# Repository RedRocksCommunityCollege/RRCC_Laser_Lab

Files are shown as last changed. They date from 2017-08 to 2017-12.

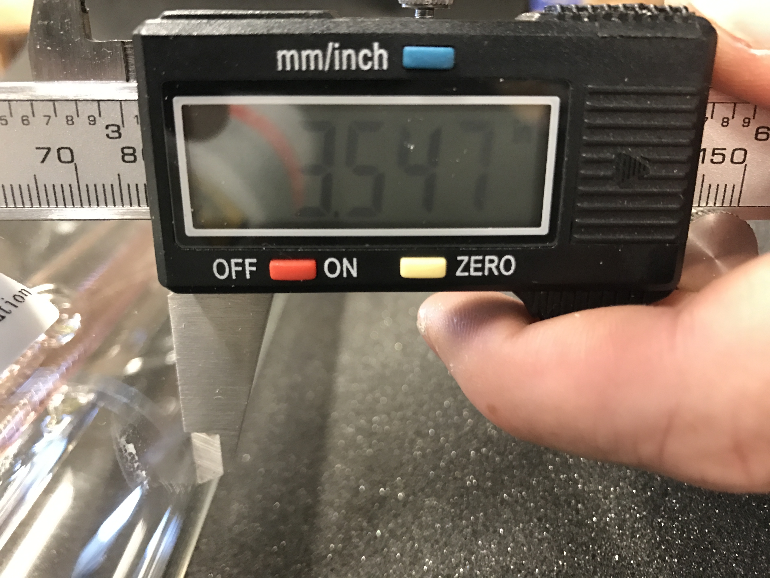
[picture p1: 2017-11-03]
Laser_Build_Pictures/47_Tube_Right_Middle_Outside_Diameter_Detail.JPG

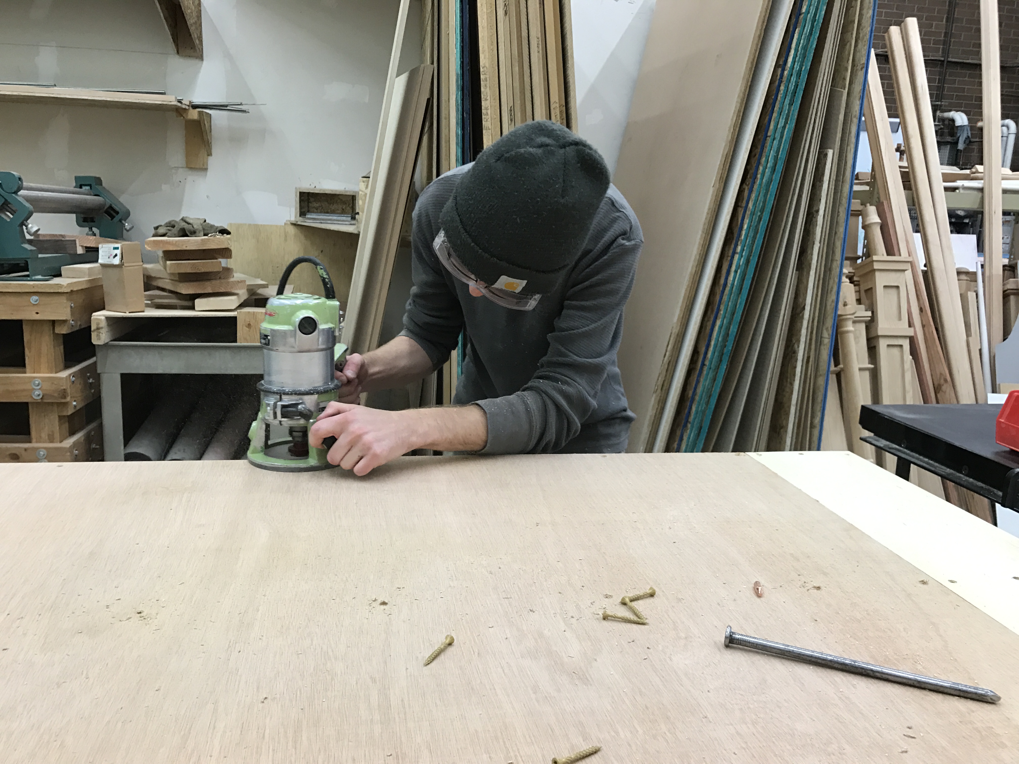
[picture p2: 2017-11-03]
Laser_Build_Pictures/6_Laser_Table_Build.JPG

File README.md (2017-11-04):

## Welcome to the RRCC Laser GitHub Page. Below you will find links and information for the attached repo.

**Background Information** : Over the fall of 2017 the students of Red Rocks Community College designed and build an 80 watt computer controlled laser cutter. The process took around 12 weeks working 4 to 8 hours a week. The parts were ordered from:

* Gantry parts: https://openbuilds.com/
* Laser parts: http://www.lightobject.com/
* Building table parts: https://www.homedepot.com/
* Other: https://www.amazon.com/

***

The parts list can be found here: [Parts List](https://github.com/RedRocksCommunityCollege/RRCC_Laser_Lab/tree/master/Parts_List). We have included both an Excel and .csv file for both the gantry and laser parts list. 

The image files can be found here: [Laser build pictures](https://github.com/RedRocksCommunityCollege/RRCC_Laser_Lab/tree/master/Laser_Build_Pictures). The images have a basic description in the file name. They are in chronological order and images that have a measurement in it should have a close-up that follows the wide image.  

The project timeline and To Do can be found here: [Timeline and ToDo](https://github.com/RedRocksCommunityCollege/RRCC_Laser_Lab/projects/1). In the Projects tab you will find all the ongoing issues that we are working on. If you would like to work on one of these isseus feel free to assign the issue to yourself and move it the the active column. Once you are finished please move the issue to the Done column and mark the issue as closed in the issues tab. We are using the following code for issues:

* **Bug** is software related issue (Eg make a wiki, Work on GitHub, add files...)
* **Enhancement** is for physical modifications to the Laser cutter.
* **Question** is for elements that need leadership approval. 

***

The tube that we are using is a [W2 Reci laser tube](http://www.recilaser.com/en/index.php?m=&c=Index&a=show&catid=7&id=66) that has a wattage of 90. We are using an [800 Watt chiller](http://www.lightobject.com/LightObject-800W-Water-Chiller-for-CO2-Laser-Machine-AC110V-60Hz-P996.aspx) and a [Smoothieboard v1](http://smoothieware.org/smoothieboard) control board. 

  

***
The main goal of the laser cutter is to be a tool for student working in the lab as well as a tool for students to use for projects in classes. The cutter will be able to cut wood and leather and engrave metal. We are also hoping to be able to...

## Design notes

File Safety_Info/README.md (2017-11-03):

# Safety_Info
These are all the files from Reci. We are using the W2 laser in this build. [Here is a link to the product page](http://www.recilaser.com/en/index.php?m=&c=Index&a=show&catid=7&id=66)

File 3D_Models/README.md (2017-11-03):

# 3D-Models

These files are used for virtual assemblies, visualizing parts, and creating test simulations

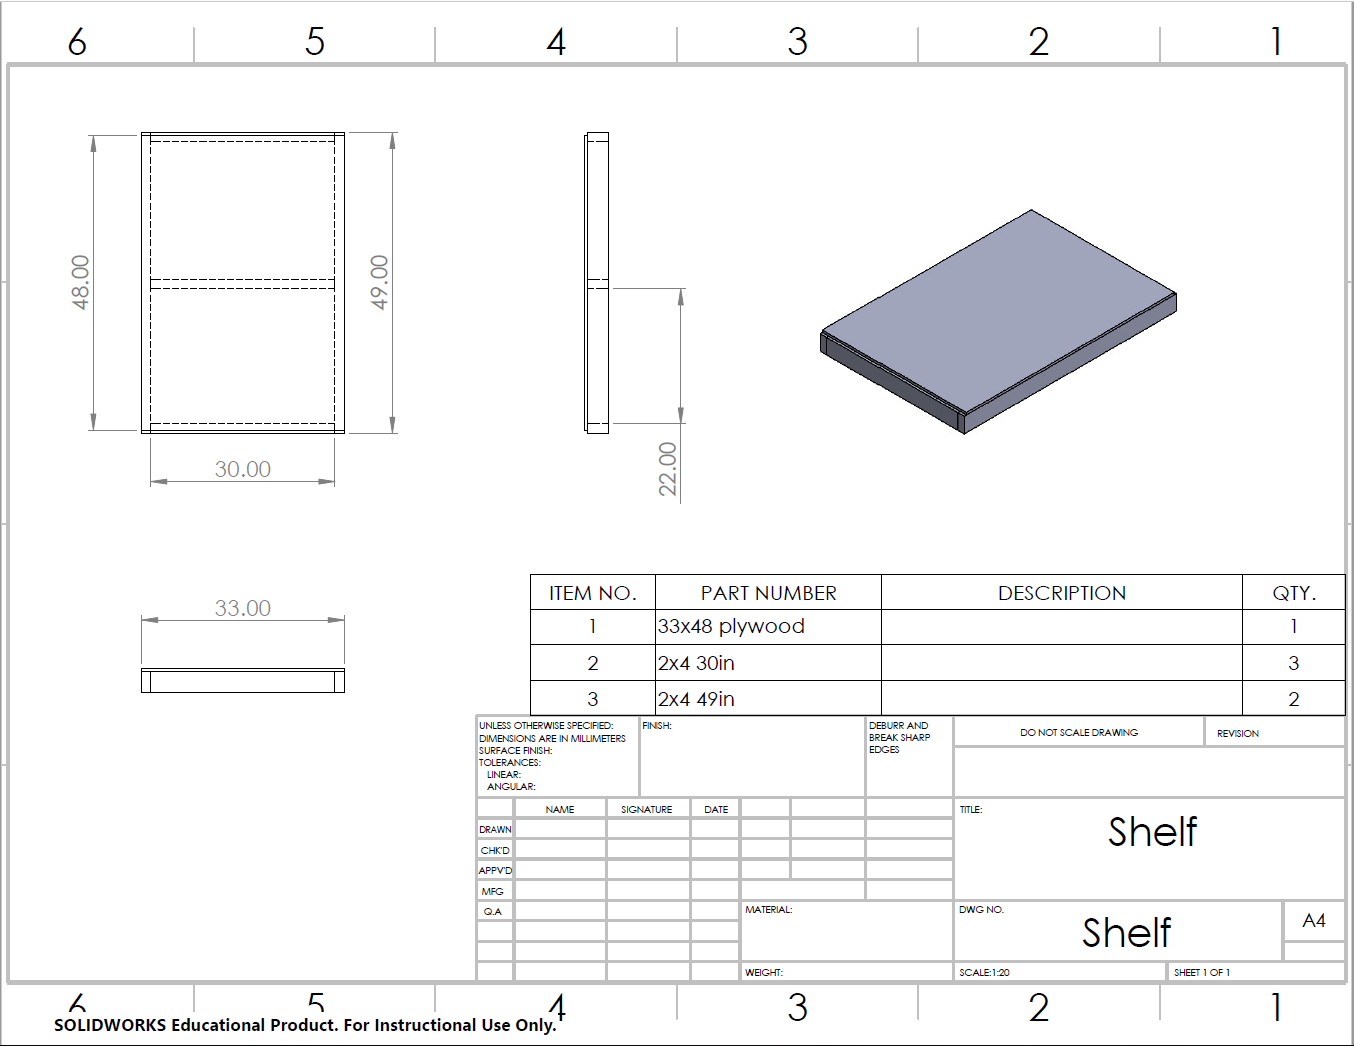
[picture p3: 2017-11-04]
Tech_Drawings_Specifications/Shelft.PNG

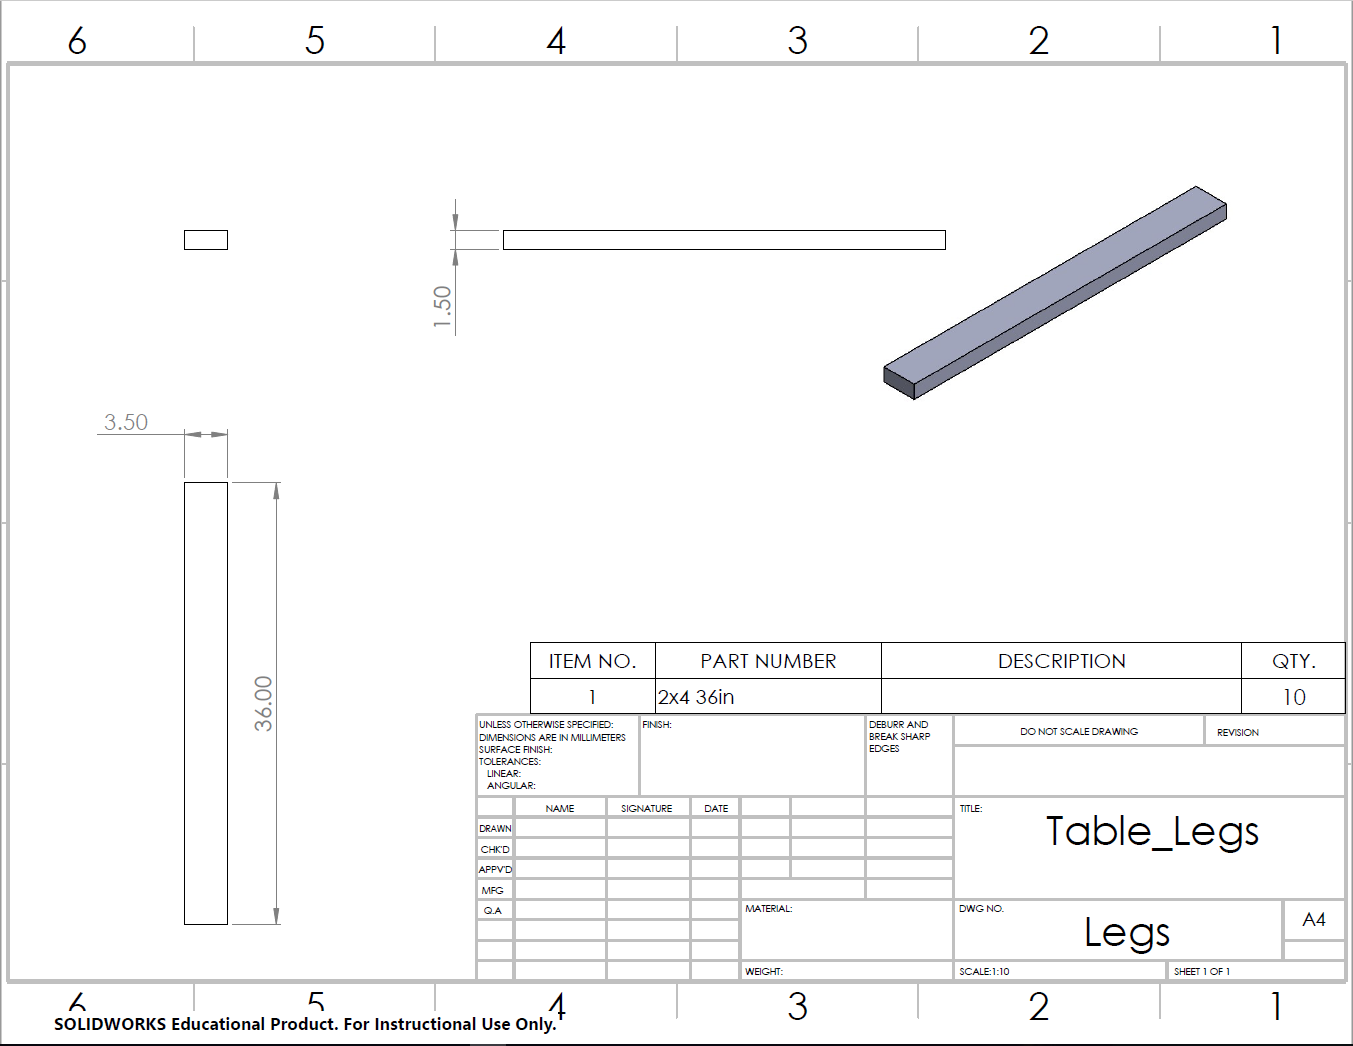
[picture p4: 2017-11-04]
Tech_Drawings_Specifications/Leg.PNG

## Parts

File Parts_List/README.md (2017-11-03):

# Parts_List

List of all necessary components for both the gantry and laser parts

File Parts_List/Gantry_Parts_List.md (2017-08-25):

Item,	Item, Description,	URL,	Quantity, 	Unit Price,	Total,
C-Beam Linear Actuator Bundle	1000mm, Include Motor,	http://openbuildspartstore.com/c-beam-linear-actuator-bundle/ ,	3,	139.95,	419.85,
V-Slot Linear Rail 20mm x 60mm	20mm x 60mm, 1000mm, Silver	http://openbuildspartstore.com/v-slot-linear-rail/ ,	8,	17,	136,
V-Slot Linear Rail 20mm x 80mm	20mm x 80mm, 1000mm, Silver	http://openbuildspartstore.com/v-slot-linear-rail/ ,	1,	22,	22,
Black Angle Corner Connector	Corner Connectors,	http://openbuildspartstore.com/black-angle-corner-connector/ ,	50,	2.75,	137.5,
Cube Corner Connector	3-Way Corner Connector,	http://openbuildspartstore.com/cube-corner-connector/ ,	15, 3.25,	48.75,
Tee Nuts (25 Pack),	Tee Nuts,	http://openbuildspartstore.com/tee-nuts-25-pack/ ,	5,	4.95,	24.75,
Smothieboard 4x	Control Board,	https://shop.uberclock.com/collections/smoothie/products/smoothieboard-4x ,	1,	129.95,	129.95,
Low Profile M5 Screws	8mm M5 Screw,	http://openbuildspartstore.com/low-profile-screws-m5/ ,	4,	3 , 12,
12V/29A Meanwell Power Supply	Power, supply for motors/ logic board,	http://openbuildspartstore.com/12v-29a-meanwell-power-supply/ ,	1,	47.95,	47.95

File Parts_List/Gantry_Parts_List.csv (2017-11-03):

Item | Item Description | URL | Quantity | Unit Price | Total
C-Beam Linear Actuator Bundle | 1000mm, Include Motor | http://openbuildspartstore.com/c-beam-linear-actuator-bundle/ | 3 | 139.95 | 419.85
V-Slot Linear Rail 20mm x 60mm | 20mm x 60mm 1000mm Silver | http://openbuildspartstore.com/v-slot-linear-rail/ | 8 | 17 | 136
V-Slot Linear Rail 20mm x 80mm | 20mm x 80mm 1000mm Silver | http://openbuildspartstore.com/v-slot-linear-rail/ | 2 | 22 | 44
Black Angle Corner Connector | Corner Connectors | http://openbuildspartstore.com/black-angle-corner-connector/ | 75 | 2.75 | 206.25
Cube Corner Connector | 3-Way Corner Connector | http://openbuildspartstore.com/cube-corner-connector/ | 15 | 3.25 | 48.75
Tee Nuts (25 Pack) | Tee Nuts | http://openbuildspartstore.com/tee-nuts-25-pack/ | 7 | 4.95 | 34.65
Smothieboard 4x | Smoothieboard 5xC v1.1 | http://openbuildspartstore.com/smoothieboard-5xc-v1-1/ | 2 | 165.95 | 331.9
Low Profile M5 Screws | 8mm M5 Screw | http://openbuildspartstore.com/low-profile-screws-m5/ | 7 | 3 | 21
12V/29A Meanwell Power Supply | Power supplie for motors/ logic board | http://openbuildspartstore.com/12v-29a-meanwell-power-supply/ | 1 | 47.95 | 47.95
V-Slot Linear Rail 20mm x 60mm | 20mm x 60mm 1500mm Silver | http://openbuildspartstore.com/v-slot-linear-rail/ | 2 | 23 | 46
90 Degree Joining Plate | Connect X axis to Y axis | http://openbuildspartstore.com/90-degree-joining-plate/ | 2 | 4.8 | 9.6
 |  |  |  |  | 1345.95

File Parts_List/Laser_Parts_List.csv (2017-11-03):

Item Description | SKU | URL | Quantity | Unit Price | Total
80W~100W PWM CO2 Laser Power Supply (AC110V) | LSR-JN80WCO2-1V | www.lightobject.com | 1 | 285 | 285
LightObject 800W Water Chiller for CO2 Laser Machine (AC110V 60Hz) | WC-LO850W1V6 | www.lightobject.com | 1 | 525 | 525
CO2 10600nm Laser Eyes Protection Glasses/Goggle. CE certified | LSR-EP4 | www.lightobject.com | 3 | 35 | 105
Laser Head Mount for 25mm Mirror & 20mm Focus Lens. LR Type | LSR-YT-HD2520LR | www.lightobject.com | 1 | 59 | 59
Improved 20mm ZnSe Focus lens (F50.8mm) | LSR-LEN20ZN5I | www.lightobject.com | 1 | 35 | 35
Pro 20mm Reflection Mirror Mount for Co2 Laser Machine | LSR-PR20M2D | www.lightobject.com | 34.5 | 2 | 69
20 mm Molybdenum (MO) Reflection Mirror | LSR-MIR20MO | www.lightobject.com | 2 | 27.5 | 55
25mm High Quality Si Plated Reflection Mirror | LSR-MIR25MSI | www.lightobject.com | 1 | 29.5 | 29.5
High Quality RECI W2 80W CO2 Sealed Laser Tube(10000Hrs) | LSR-JLDHQ80WCO2 | www.lightobject.com | 1 | 650 | 650
http://www.lightobject.com/3-digit-Mini-Blue-LED-1A-Current-Meter-P641.aspx | EPM-3D1AB | www.lightobject.com | 1 | 9.5 | 9.5

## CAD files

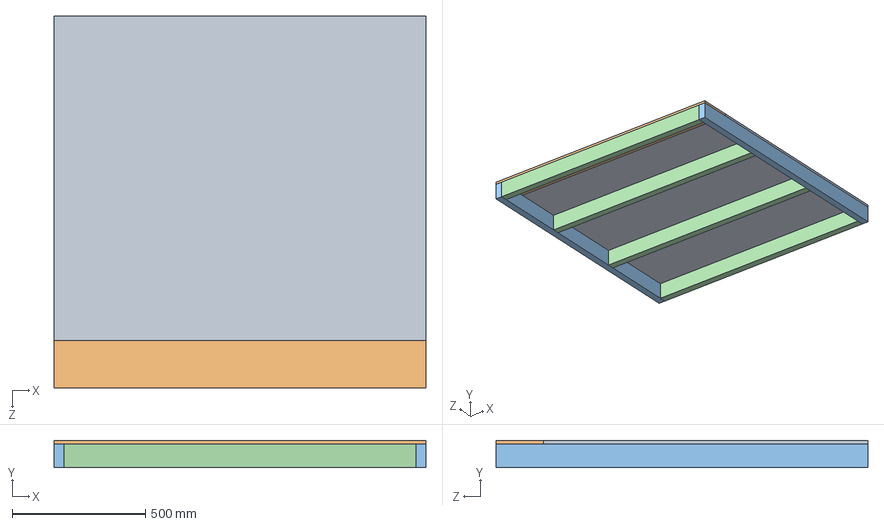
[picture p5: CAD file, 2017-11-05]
3D_Models/Top.SLDASM
1397.0 x 101.6 x 1397.0 mm
48x55 plywood
7x55 plywood
2x4 55in x 2
2x4 52in x 4

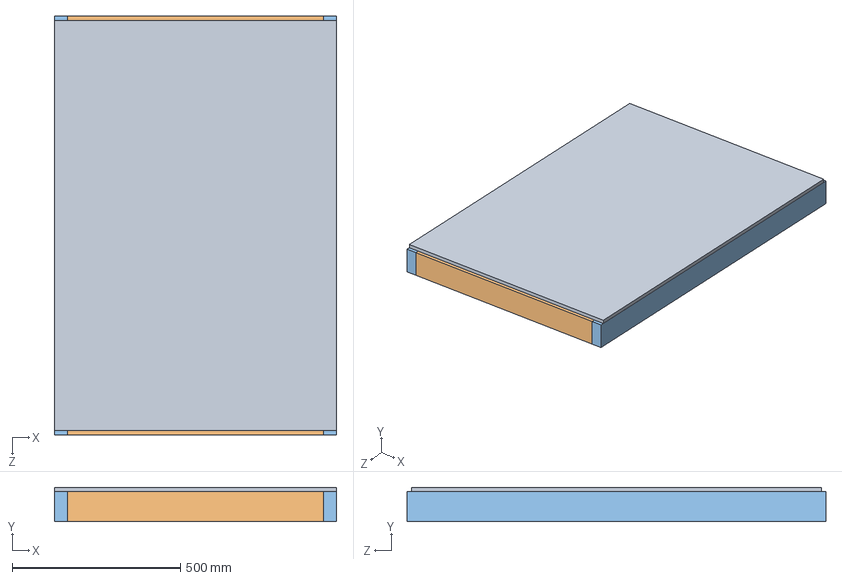
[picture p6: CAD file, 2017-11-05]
3D_Models/Shelf.SLDASM
838.2 x 101.6 x 1244.6 mm
33x48 plywood
2x4 30in x 3
2x4 49in x 2

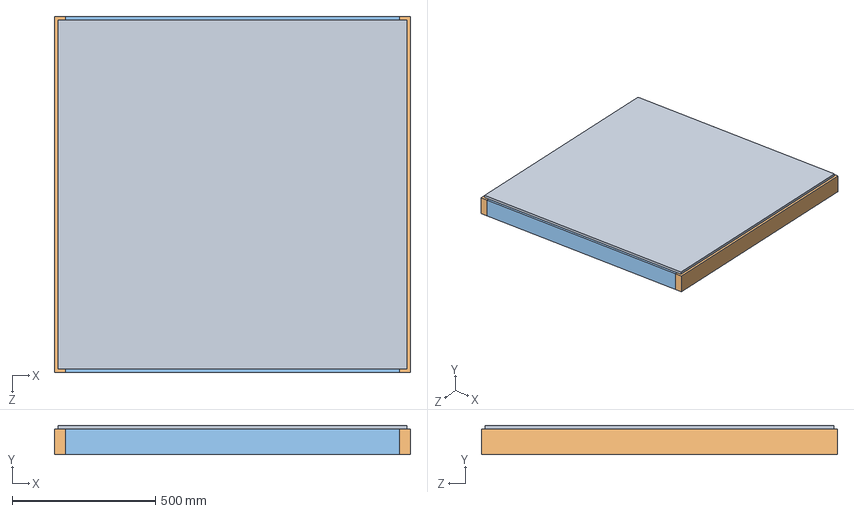
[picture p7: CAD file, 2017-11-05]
3D_Models/Bottom_Shelf.SLDASM
1244.6 x 101.6 x 1244.6 mm
48x48 plywood
2x4 49in x 2
2x4 46in x 3

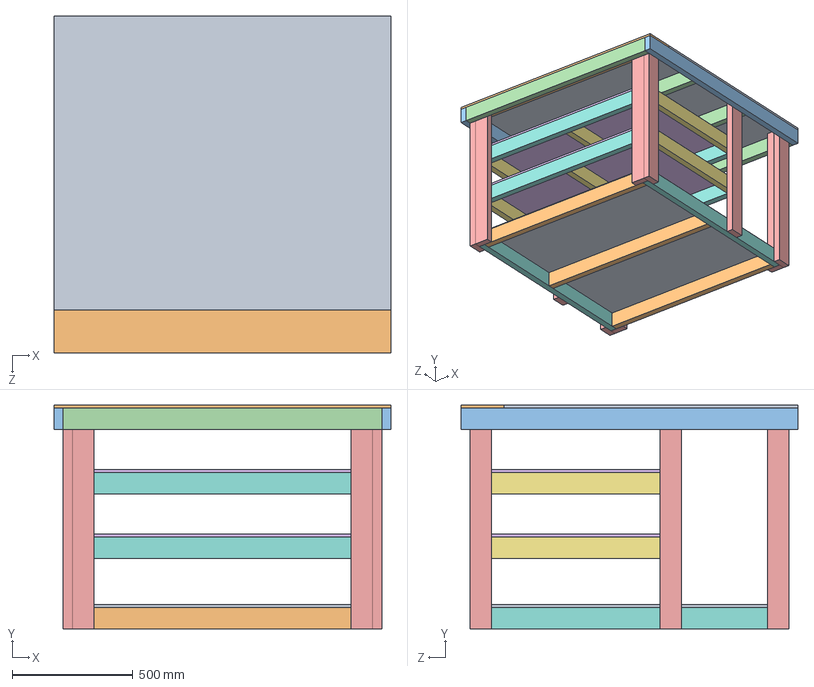
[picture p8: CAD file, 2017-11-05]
3D_Models/CNC_Laser_Table_Assembly.SLDASM
1397.0 x 927.1 x 1397.0 mm
48x55 plywood
7x55 plywood
2x4 55in x 2
2x4 52in x 4
2x4 36in x 10
33x48 plywood x 2
2x4 30in x 6
2x4 49in x 6
48x48 plywood
2x4 46in x 3

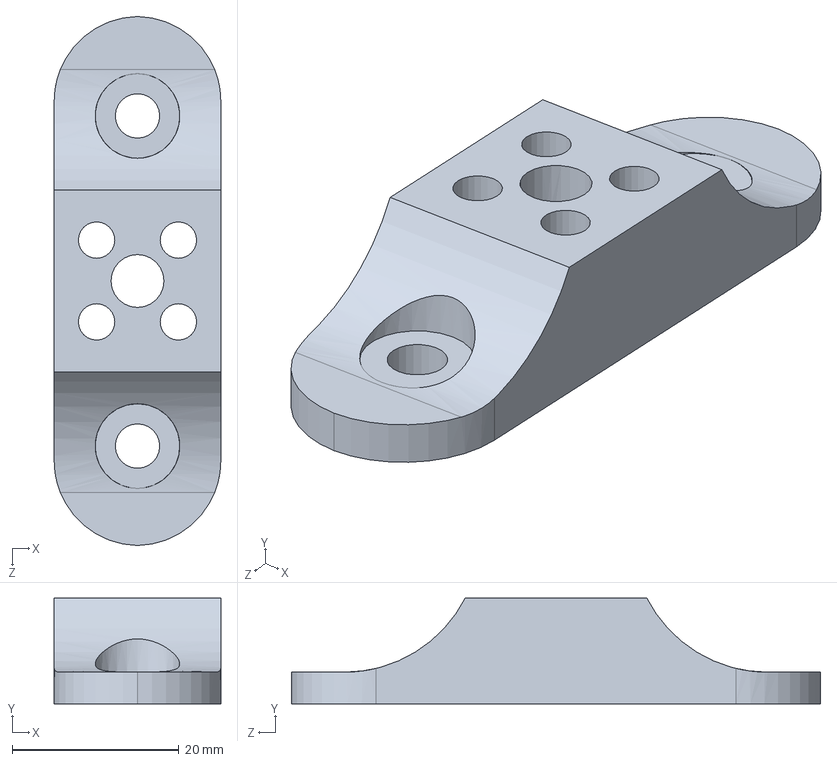
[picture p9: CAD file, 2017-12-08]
3D-Printed_Components/Mirror_Mount_Y_Axis.SLDPRT
20.0 x 12.7 x 63.5 mm

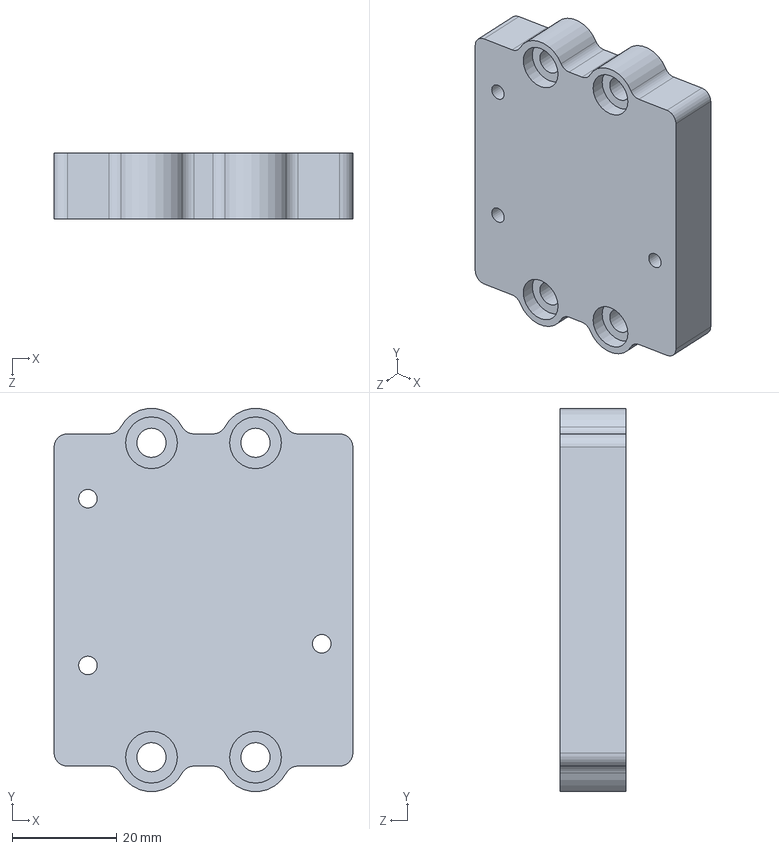
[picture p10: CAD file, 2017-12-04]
3D-Printed_Components/CNC_Laser_Adapter_Plate.SLDPRT
57.1 x 73.2 x 12.7 mm

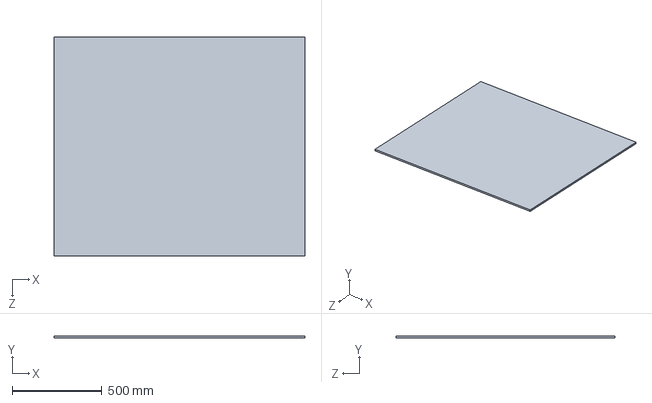
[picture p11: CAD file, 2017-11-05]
3D_Models/48x55 plywood.SLDPRT
1397.0 x 12.7 x 1219.2 mm

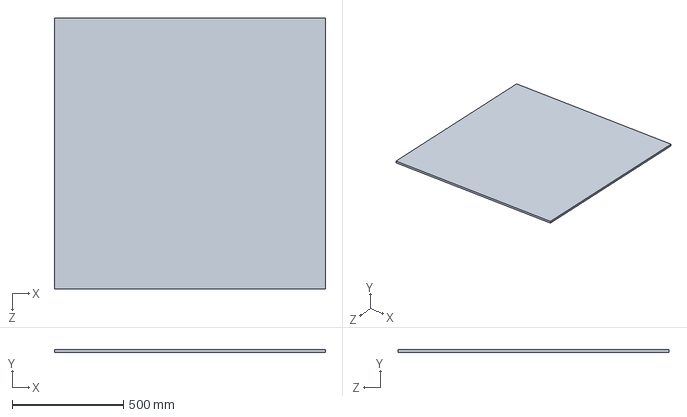
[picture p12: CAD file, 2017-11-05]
3D_Models/48x48 plywood.SLDPRT
1219.2 x 12.7 x 1219.2 mm

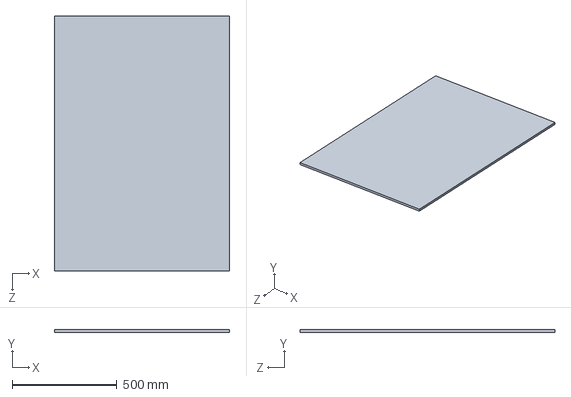
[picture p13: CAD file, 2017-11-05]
3D_Models/33x48 plywood.SLDPRT
838.2 x 12.7 x 1219.2 mm

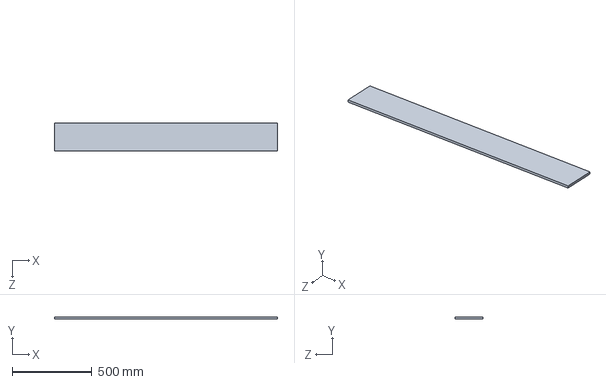
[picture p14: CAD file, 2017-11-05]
3D_Models/7x55 plywood.SLDPRT
1397.0 x 12.7 x 177.8 mm

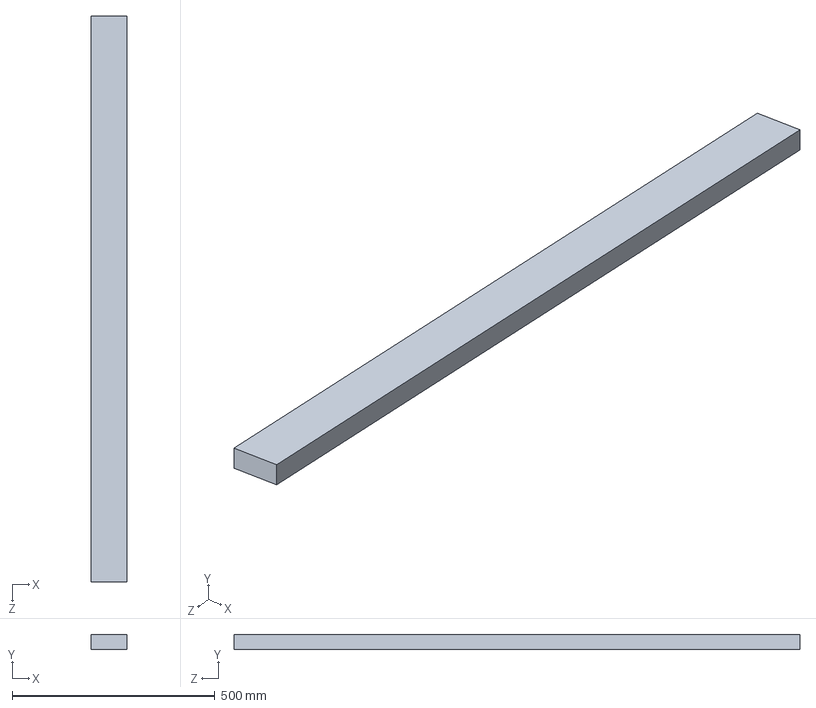
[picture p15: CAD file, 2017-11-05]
3D_Models/2x4 55in.SLDPRT
88.9 x 38.1 x 1397.0 mm

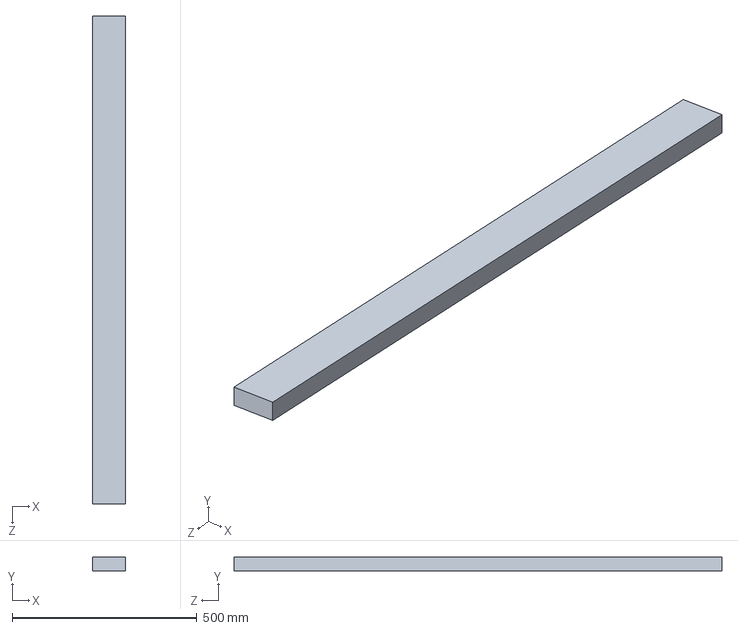
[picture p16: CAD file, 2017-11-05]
3D_Models/2x4 52in.SLDPRT
88.9 x 38.1 x 1320.8 mm

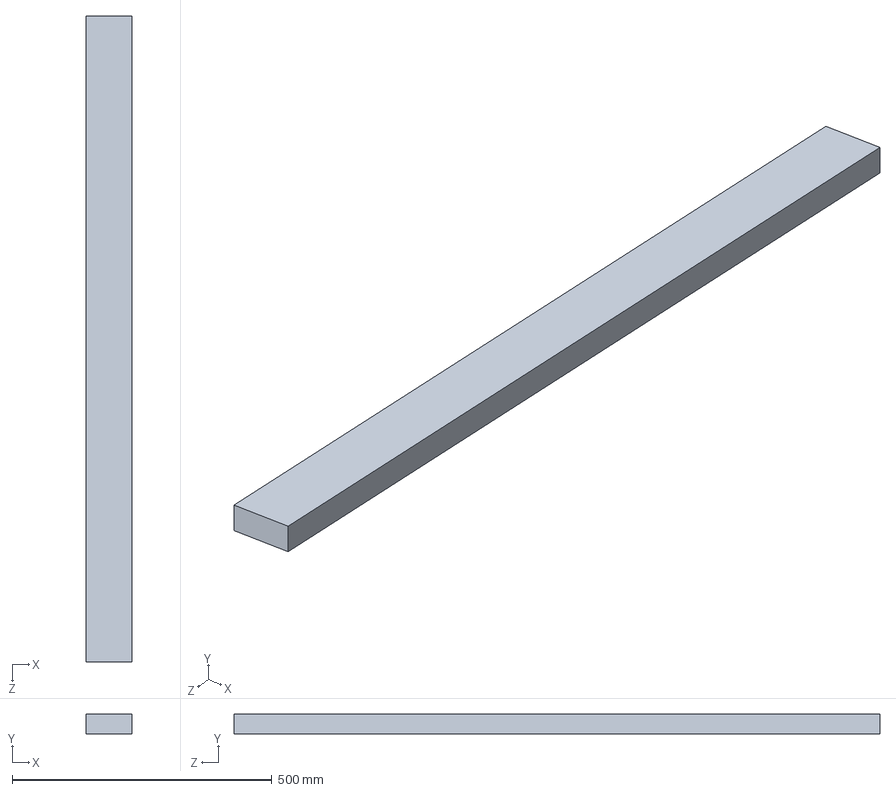
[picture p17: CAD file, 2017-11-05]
3D_Models/2x4 49in.SLDPRT
88.9 x 38.1 x 1244.6 mm

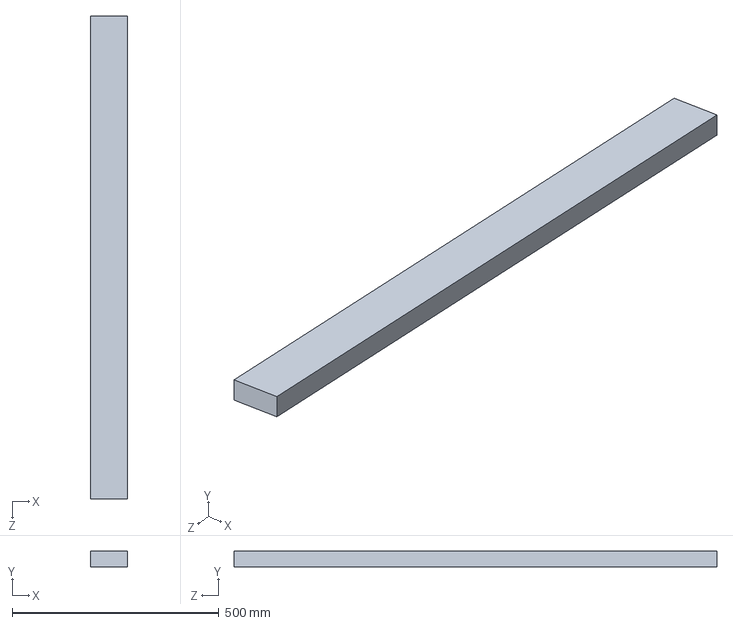
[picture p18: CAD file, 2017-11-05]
3D_Models/2x4 46in.SLDPRT
88.9 x 38.1 x 1168.4 mm

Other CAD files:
3D-Printed_Components/Mirror_Mounts.SLDPRT
3D_Models/2x4 36in.SLDPRT
3D_Models/2x4 30in.SLDPRT
3D_Models/Xrail_20x20mm.SLDPRT
3D-Printed_Components/CNC_Laser_Adapter_Plate.STL
3D-Printed_Components/Mirror_Mount_Y_Axis.STL
3D-Printed_Components/Mirror_Mounts.STL
3D_Models/CNC_Laser_Mount.SLDPRT
3D_Models/Cbeam.SLDPRT
3D_Models/Cbeam.STL
3D_Models/Corner_Connector.SLDPRT
3D_Models/Corner_Connector.STL
3D_Models/M5_8mm_Screw.SLDPRT
3D_Models/M5_8mm_Screw.STL
3D_Models/Tee_Nut.SLDPRT
3D_Models/Tee_Nut.STL
3D_Models/Xrail_20x20mm.STL
Tech_Drawings_Specifications/Bottom_Shelf.SLDDRW
Tech_Drawings_Specifications/Legs.SLDDRW
Tech_Drawings_Specifications/Shelf.SLDDRW
Tech_Drawings_Specifications/Table_Top.SLDDRW

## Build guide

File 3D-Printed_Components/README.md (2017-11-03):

# 3D-Printed_Components

These files are 3D-Printed parts for the CNC Laser

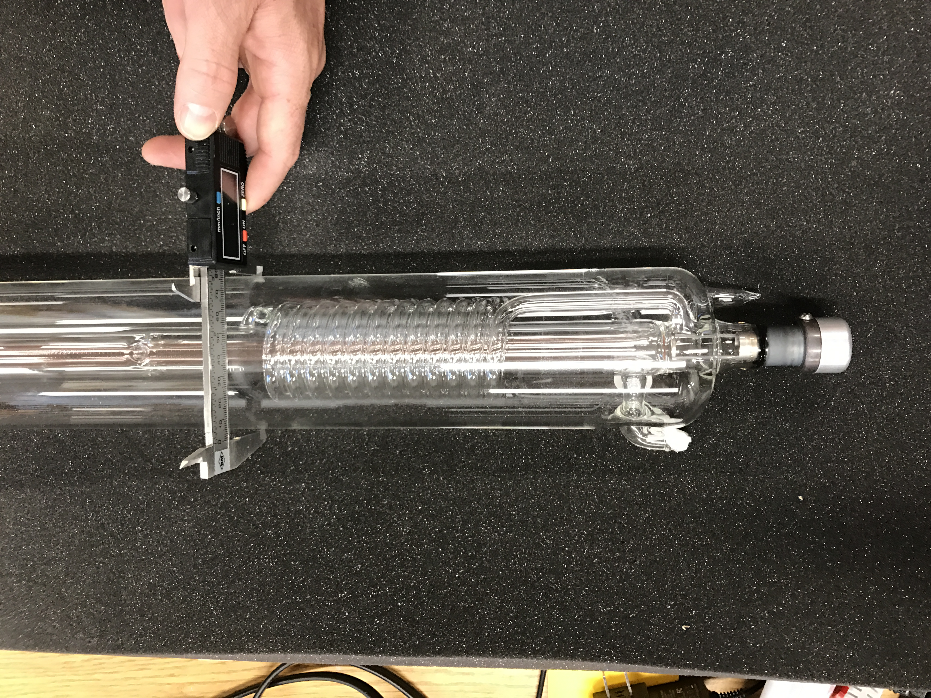
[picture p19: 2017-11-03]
Laser_Build_Pictures/48_Tube_Left_Middle_Outside_Diameter.JPG

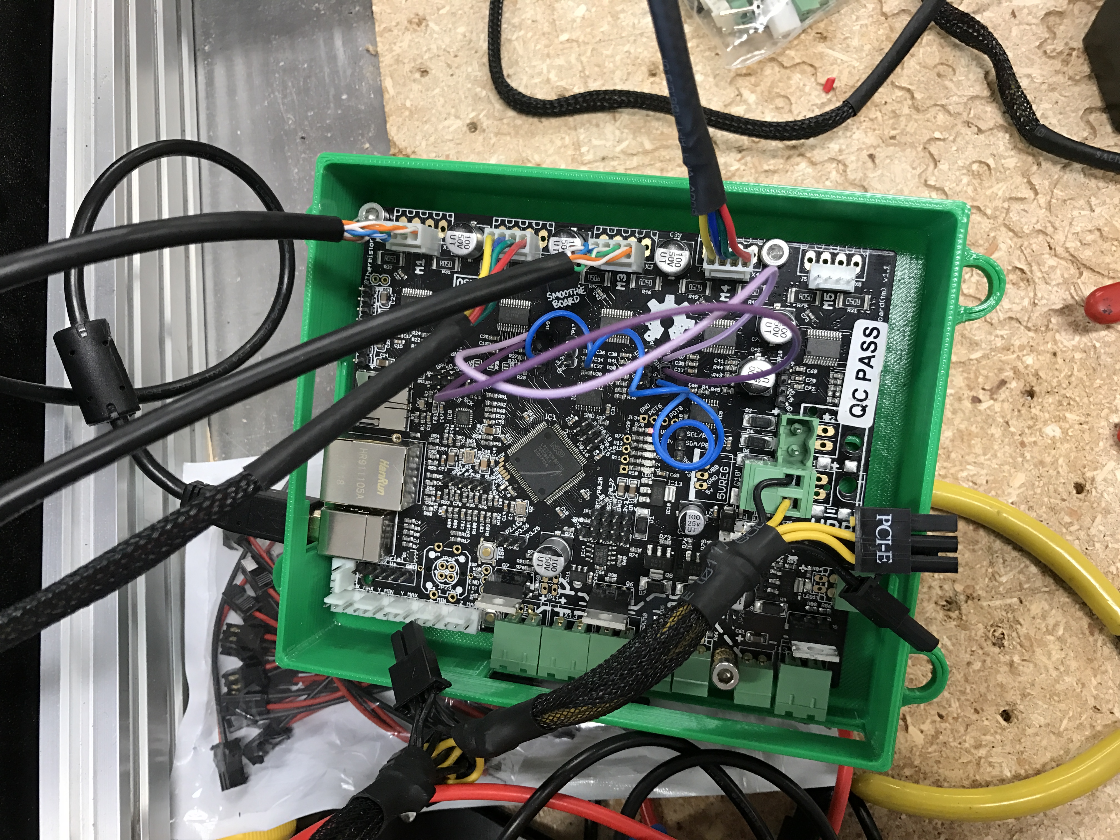
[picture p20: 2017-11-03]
Laser_Build_Pictures/20_New_Motherboard_and_Box_in_Use.JPG

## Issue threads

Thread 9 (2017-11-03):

Get CAM Software

AForland, 2017-11-03:

endlesstankzone, 2017-11-27:
After doing some research i believe i found a good opensource option for the laser cutter cam software. After downloading a few free open source software suites, the best one i was able to find was a plugin for Inkscape. Inkscape is a open source vector graphics editor that open source and free to use. Because its opensource many people have created plugins for various things. A company by the name of J tech Photonics has created a plugin for Inkscape that lets you cut/engrave images or DXF/DWG files easily through there plugin. I tested a couple of things like text, images, and shapes and it appears to be turning the laser on and off correctly and moving the machine around in a predictable way.

Inkscape: https://inkscape.org/en/

Laser Plugin: https://jtechphotonics.com/?page_id=2012

Closed 2017-11-27.

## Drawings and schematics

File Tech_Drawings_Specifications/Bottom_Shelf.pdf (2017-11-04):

6

5

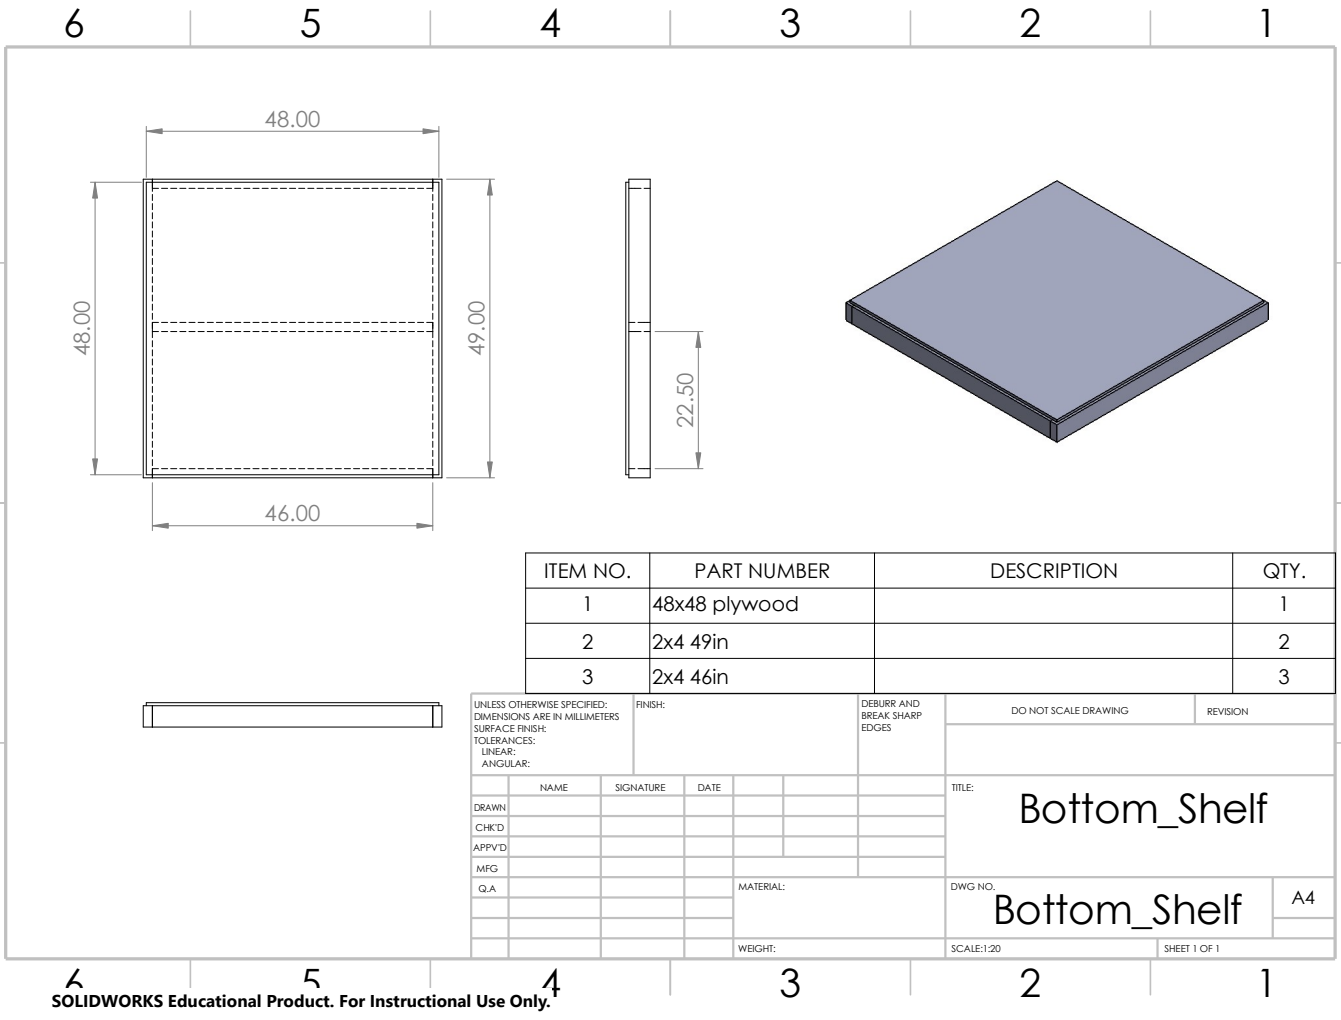
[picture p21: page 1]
WEIGHT:; SCALE:1:20; SHEET 1 OF 1; Bottom_Shelf ²².50 48.00

ITEM NO. | PART NUMBER | DESCRIPTION | QTY.
1 | 48x48 plywood | | 1
2 | 2x4 49in | | 2
3 | 2x4 46in | | 3

DIMENSIONS ARE IN MILLIMETERS SURFACE FINISH: TOLERANCES: LINEAR: ANGULAR: | FINISH: | DEBURR AND BREAK SHARP EDGES | DO NOT SCALE DRAWING UNLESS OTHERWISE SPECIFIED: | REVISION

NAME | SIGNATURE | DATE | | | | TITLE:

DRAWN
CHK'D
APPV'D
Q.A | | | | MATERIAL: | DWG NO. Bottom_Shelf | A4

MFG

SOLIDWORKS Educational Product. For Instructional Use Only.

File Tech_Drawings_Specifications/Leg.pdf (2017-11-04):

6

5

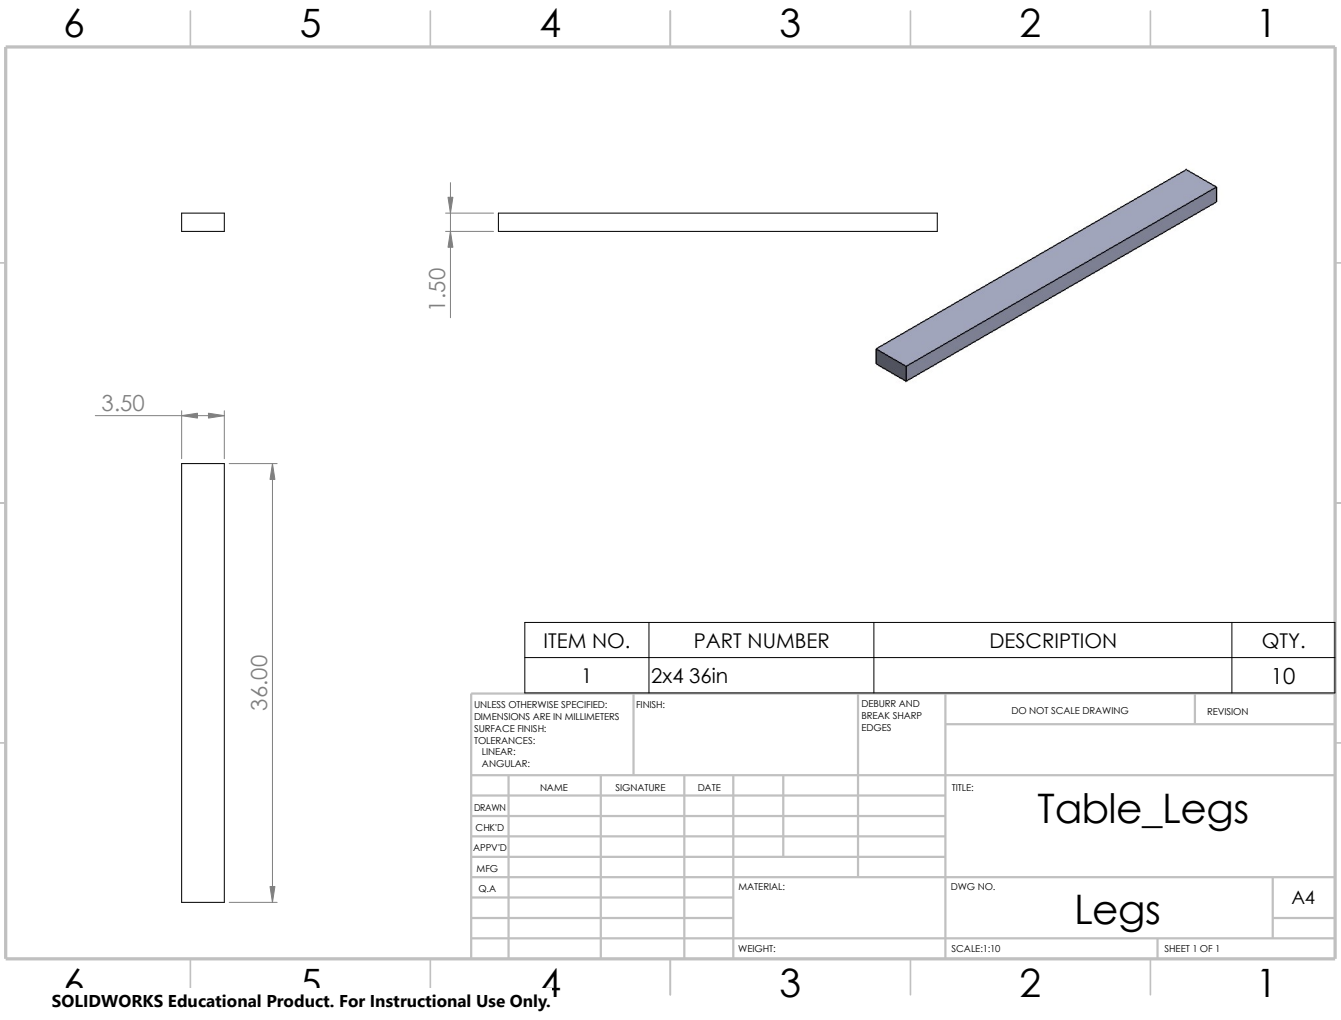
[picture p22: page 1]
WEIGHT:; SCALE:1:10; SHEET 1 OF 1

ITEM NO. | PART NUMBER | DESCRIPTION | QTY.
1 | 2x4 36in | | 10

UNLESS OTHERWISE SPECIFIED: DIMENSIONS ARE IN MILLIMETERS SURFACE FINISH: TOLERANCES: LINEAR: ANGULAR: | FINISH: | DEBURR AND BREAK SHARP EDGES | DO NOT SCALE DRAWING | REVISION

NAME | SIGNATURE | DATE | | | | TITLE: Table_Legs

DRAWN
CHK'D
APPV'D
Q.A | | | | MATERIAL: | DWG NO. Legs | A4

MFG

SOLIDWORKS Educational Product. For Instructional Use Only.

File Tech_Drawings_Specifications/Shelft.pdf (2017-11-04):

6

5

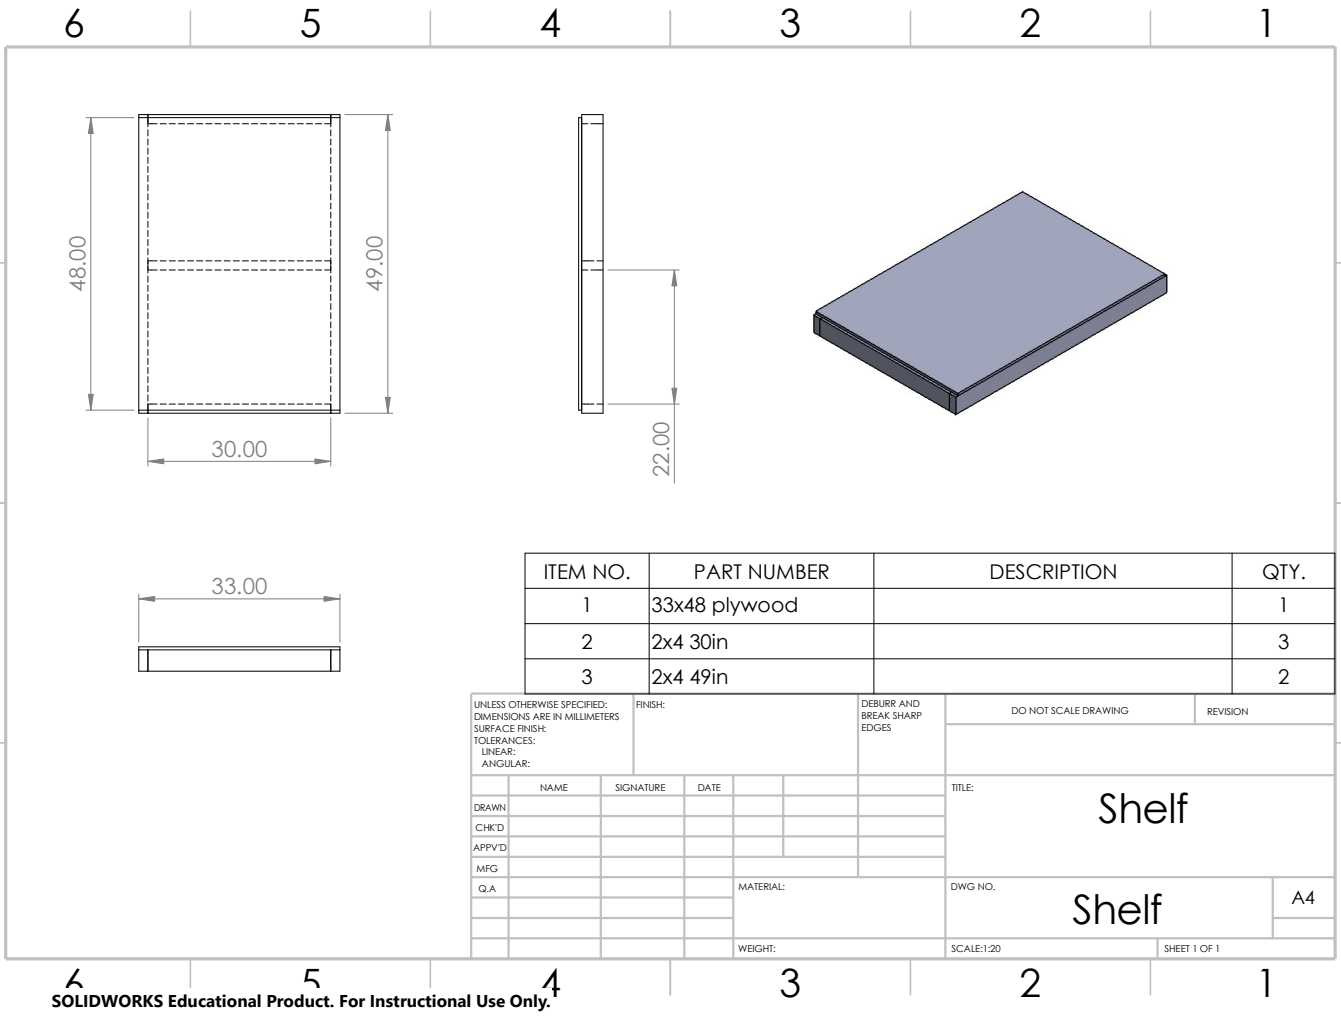
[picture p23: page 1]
WEIGHT:; SCALE:1:20; SHEET 1 OF 1

ITEM NO. | PART NUMBER | DESCRIPTION | QTY.
1 | 33x48 plywood | | 1
2 | 2x4 30in | | 3
3 | 2x4 49in | | 2

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

NAME | SIGNATURE | DATE | | | | TITLE: Shelf

DRAWN
CHK'D
APPV'D
Q.A | | | | MATERIAL: | DWG NO. Shelf | A4

MFG

SOLIDWORKS Educational Product. For Instructional Use Only.

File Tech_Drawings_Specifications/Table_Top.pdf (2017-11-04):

6

5

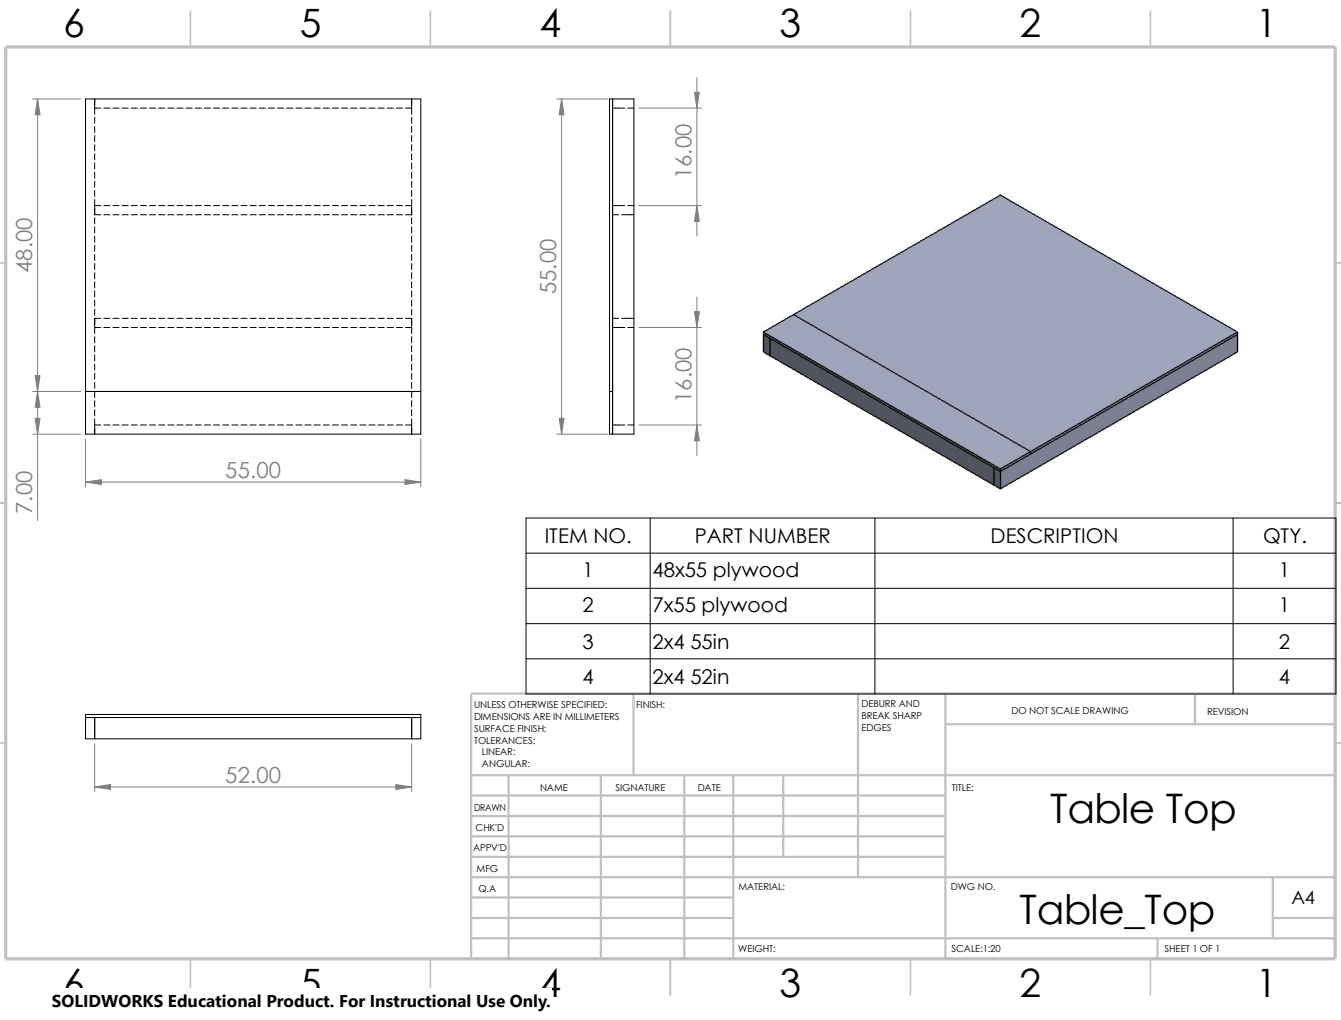
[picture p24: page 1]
WEIGHT:; SCALE:1:20; SHEET 1 OF 1

Table Top ⁴⁸.00

ITEM NO. | PART NUMBER | DESCRIPTION | QTY.
1 | 48x55 plywood | | 1
2 | 7x55 plywood | | 1
3 | 2x4 55in | | 2
4 | 2x4 52in | | 4

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

NAME | SIGNATURE | DATE | | | | TITLE:

DRAWN
CHK'D
APPV'D
Q.A | | | | MATERIAL: | DWG NO. Table_Top | A4

MFG

SOLIDWORKS Educational Product. For Instructional Use Only.

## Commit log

2017-07-25 Drawings and schematics
2017-07-25 Files to be cut
2017-07-26 Add files via upload
    Gantry V1.0
2017-08-24 Parts list including where to purchase, item priceing, and quantitys needed
    [Gantry_Parts_List.xlsx]
2017-08-25 All the parts needed for the laser, see gantry parts list for additinal components.
    [Laser parts list.xlsx]
2017-08-25 Updated parts list for the gantry
    [Gantry_Parts_List.xlsx]
2017-09-01 Updated Laser parts list with url
    [Laser_parts_list.xlsx]
2017-09-12 Updated the parts list to include smothie board from openbuilds
    [Gantry_Parts_List.xlsx]
2017-09-15 Updated Parts List
    [Gantry_Parts_List.xlsx]
2017-09-18 updaed parts list
    [Gantry_Parts_List.xlsx]
2017-10-21 Files from RECI for our tube
2017-11-03 Added pictures of Laser build
2017-11-03 Added usefull models
    [Cbeam.SLDPRT, Corner_Joint.SLDPRT, Xrail.SLDPRT]
2017-11-03 Added Tee Nuts
    [Tee_Nut.SLDPRT]
2017-11-03 STL file for CBEAM
    [Cbeam.STL]
2017-11-03 STL file for Tee Nut
    [Tee_Nut.STL]
2017-11-03 Solidworks File for Corner Connector
    [Corner_Connector.SLDPRT]
2017-11-03 STL file for Corner Connector
    [Corner_Connector.STL]
2017-11-03 Solidworks File for C-Beam
    [Cbeam.SLDPRT]
2017-11-03 Solidworks File for M5 8MM Screw
    [M5_8mm_Screw.SLDPRT]
2017-11-03 Solidworks File for Tee Nut
    [Tee_Nut.SLDPRT]
2017-11-03 Solidworks File for 20x20 MM X-Rail
    [Xrail.SLDPRT]
2017-11-03 STL file for Xrail 20x20 MM X-Rail
    [Xrail_20x20mm.STL]
2017-11-03 STL File for M5 8MM Screw
    [M5_8mm_Screw.STL]
2017-11-03 Solidworks Files for CNC Laser Tube Mount
    [CNC_Laser_Mount.SLDPRT]
2017-11-03 STL Files for CNC Laser Tube Mount
2017-11-03 Updated picture folder
    [Gantry_Parts_List.xlsx, Laser parts list.xlsx, Laser_parts_list (1) (1).xlsx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]
2017-11-03 added Laser_Parts_List.csv
    [Laser_Parts_List.csv]
2017-11-03 added Gantry Parts List
    [Gantry_Parts_List.csv]
2017-11-03 Renamed Parts Lists
    [Laser parts list.xlsx, Laser_parts_list (1) (1).xlsx, Laser_parts_list (1).xlsx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]
2017-11-04 Technical drawings for CNC Laser Table
    [Bottom_Shelf.SLDDRW, Legs.SLDDRW, Shelf.SLDDRW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]
2017-11-05 Solidworks File for 30in 2x4
    [2x4 30in.SLDPRT]
2017-11-05 Solidworks File for 36in 2x4
    [2x4 36in.SLDPRT]
2017-11-05 Solidworks File for 46in 2x4
    [2x4 46in.SLDPRT]
2017-11-05 Solidworks File for 49in 2x4
    [2x4 49in.SLDPRT]
2017-11-05 Solidworks File for 52in 2x4
    [2x4 52in.SLDPRT]
2017-11-05 Solidworks File for 55in 2x4
    [2x4 55in.SLDPRT]
2017-11-05 7x55in Plywood Sheet
    [7x55 plywood.SLDPRT]
2017-11-05 33x48in Plywood Sheet
    [33x48 plywood.SLDPRT]
2017-11-05 48x48in Plywood Sheet
    [48x48 plywood.SLDPRT]
2017-11-05 48x55in Plywood Sheet
    [48x55 plywood.SLDPRT]
2017-11-05 CNC Laser Table Assembly
    [CNC_Laser_Table_Assembly.SLDASM]
2017-11-05 Bottom Shelf subassembly
    [Bottom_Shelf.SLDASM]
2017-11-05 Shelf subassembly
    [Shelf.SLDASM]
2017-11-05 Table Top subassembly
    [Top.SLDASM]
2017-12-04 3D-Printable Mirror Mounts
    [Mirror_Mounts.SLDPRT, Mirror_Mounts.STL]
2017-12-04 Laser nozle adapter plate
    [CNC_Laser_Adapter_Plate.SLDPRT, CNC_Laser_Adapter_Plate.STL]
2017-12-08 Y-Axis_ Mirror_Mount
    [Mirror_Mount_Y_Axis.SLDPRT, Mirror_Mount_Y_Axis.STL]
